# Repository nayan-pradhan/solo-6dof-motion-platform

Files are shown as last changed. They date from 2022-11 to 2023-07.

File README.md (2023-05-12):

# SOLO 6 DoF Motion Platform

motion platform (https://youtu.be/thXPA2MYcQw "6-DoF- Motion Platform")

## <u>Introduction</u>
We present an open-source 6 DoF motion platform capable of producing controlled highly dynamic motion in 3D space. The idea is to flip a quadruped robot, attach a 3D printed platform (holding the payload) to the feet, and using inverse kinematics to move the attached platform in the closed-loop kinematic chain. 12 motors works together to produce high acceleration.

Our design is based on the [open-dynamic-robot-initiative](https://github.com/open-dynamic-robot-initiative).

The platform design, pybullet simulation and robot control framework are fully open source.

1. [Hardware Framework](docs/hardware_framework.md)
2. [Software Framework](docs/software_framework.md)
3. [Setup and Notes](docs/setup_and_notes.md)
4. [Calibration and Usage](docs/calibration_and_usage.md) 
5. [Program Execution](docs/program_execution.md)
6. [Video](https://youtu.be/BtfoymwgIUY)

## <u>About the Creaters</u>
The SOLO 6 DoF Motion Platform was created at the [Dynamic Locomotion Group](https://dlg.is.mpg.de) at the [Max-Planck Institute for Intelligent Systems](https://is.mpg.de) by: 
- Nayan Man Singh Pradhan
- Patrick Frank
- An Mo

## <u>Link to Paper</u>
http://dx.doi.org/10.48550/arXiv.2303.17974

Pradhan, N. M. S., Frank, P., Mo, A., & Badri-Spröwitz, A. (2023). Upside down: affordable high-performance motion platform. arXiv preprint arXiv:2303.17974.

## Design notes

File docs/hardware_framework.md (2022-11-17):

# Hardware Framework

<p align="center">
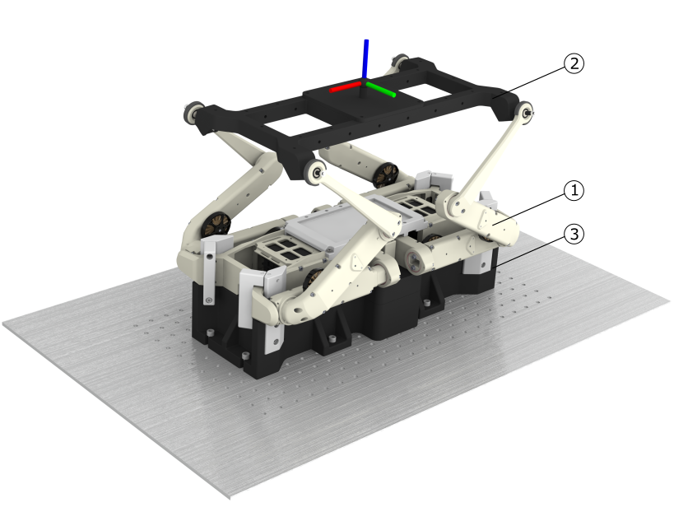
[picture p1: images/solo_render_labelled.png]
  
</p>

The hardware framework consists of three main components: 
1. the [SOLO robot](#solo-robot),
2. the [platform attached to the legs](#platform-attached-to-legs) of the SOLO robot, and
3. the [base component](#base-component) that makes sure the robot is fixed to a table.

The figure above shows the robot fixed to an optic table with the attached platform. The necessary CAD files can be found [here](../resources/CAD_files/).

### 1. SOLO robot
The SOLO 12 Robot is a quadruped robot (assembled from four legs) of total mass $2.2$ kg with a torque-controller for tracking full-body motions computed with a kino-dynamic motion optimizer \cite{herzog2016structured} \cite{ponton2018time}. The brushless actuator module used in the SOLO robot consists of a $9:1$ dual-stage timing belt transmission, a high-resolution optical encoder, and a $5000$ count-per-revolution code wheel mounted directly on the motor shaft. The desired joint torques are converted into desired motor current using the relationship $\tau_{joint}=k_{i}iN$ where $k_{i}=0.025$ Nm/A and the gear reduction $N=9$ leading to a $\tau_{joint}=0.225i$. The actuators can output $\tau_{max}=2.7$ Nm joint torque at $12$ A. More information regarding the SOLO robot can be found in the Open Dynamic Robot Initiative [Website](https://open-dynamic-robot-initiative.github.io) and their [GitHub](https://github.com/open-dynamic-robot-initiative). 
<p align="center">
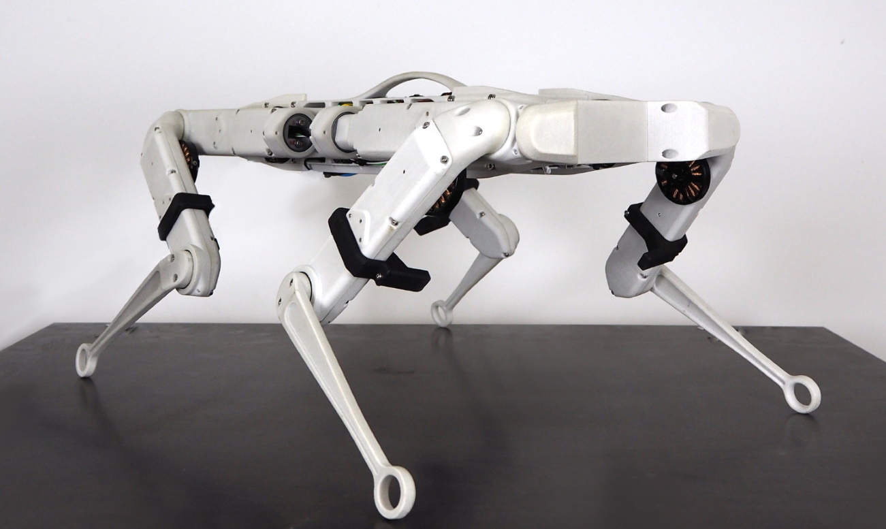
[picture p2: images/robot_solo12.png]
    
</p>
<p align="center">Solo12 Quadruped Robot. Picture source: PAL robotics.</p>

### 2. Platform Attached to Legs
The platform is mounted to the robot by four pins fixed to a spherical bearing. We used the [IGUS KGLM-05](https://www.igus.eu/product/388?C=DE&L=en&artNr=KGLM-05) spherical bearing with a maximum pivot angle of 30 degrees. These spherical bearings are press fitted to the robot legs and secured by M4 nuts on the platform. The platform itself is 3D printed while the pins are machined. There are multiple mounting points provided to attach something to the platform. All parts needed for the platform are shown in the figure below.
<p align="center">
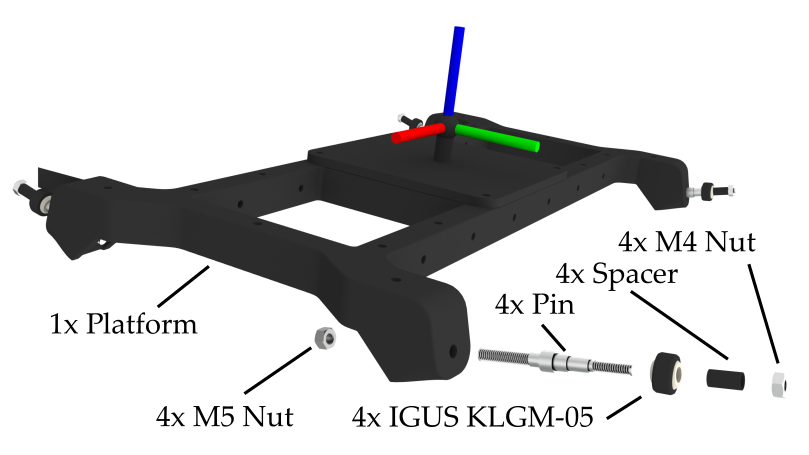
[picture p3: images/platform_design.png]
    
</p>

### 3. Base Component
To fix the robot during movement, we designed a base that is screwed on an optic table. The base consists of multiple parts, as shown in the figure below. We replaced the lower center plate of the robot with our design (No. 2), to be able to fix the robot on the base. The plate gets attached by four M3 and eight M2.5 screws to the robot and six M4 screws to the base. The base itself is fixed to the optic table by eight M6 Screws. To further support the robot base, we design clamps (No. 3, 4, 5, 6) that attach close to the hip of the robot.
<p align="center">
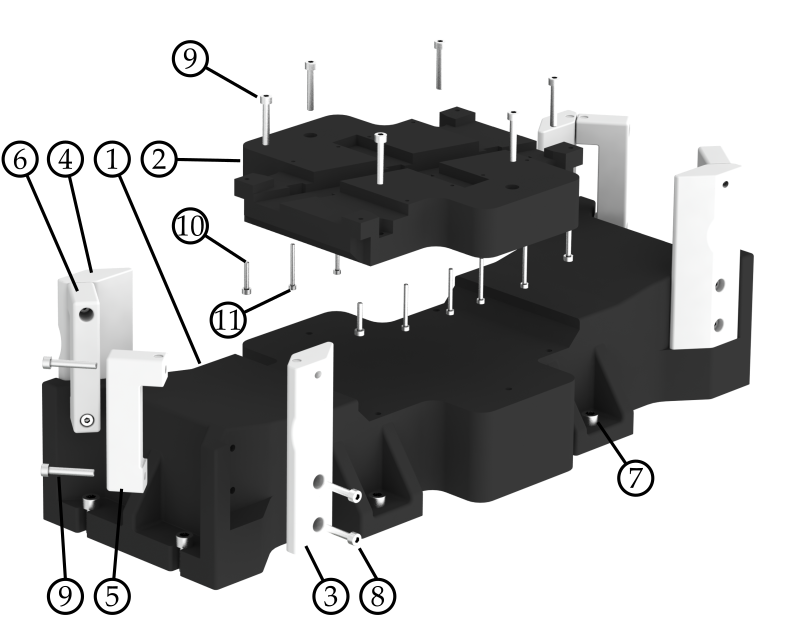
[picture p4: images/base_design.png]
    
</p>

The table below lists all the parts needed to build the base.

| No. | Name | Qty.  |
| :-----: | --- | :---: |
| 1  | Base | 1 |
| 2  | Plate Robot | 1  |
| 3 | Base Clamp | 2 |
| 4 | Base Clamp mirrored | 2 |
| 5 | Robot Clamp | 2 |
| 6 | Robot Clamp mirrored | 2  |
| 7 | SHC Screw M6x16 | 8 |
| 8 | SHC Screw M4x20 | 8 |
| 9 | SHC Screw M4x25 | 14  |
| 10 | SHC Screw M3x16 | 4  |
| 11 | SHC Screw M2.5x25 | 8  |
| 12 | HeliCoil M4 Thread Insert | 22 |

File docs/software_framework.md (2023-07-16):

# Software Framework

Our open-source software package uses the master-board from the SOLO robot [Open Dynamic Robot Initiative GitHub page](https://github.com/open-dynamic-robot-initiative) to send torque commands to the motors and read sensor data. The [master-board](https://github.com/open-dynamic-robot-initiative/master-board) centralises all the sensor and actuator data and provides wired and wireless connection to a real-time computer. 

The primary language used in our software package is Python3. The software framework is built to be modular such that any user may update, add, or remove parts of the module. As long as the modules receive an input csv file of the proper format and output the respective csv files of proper format, the software framework will work as designed. 

Our software framework consists of 4 main modules:
1. [Platform Trajectory Generation](#platform-trajectory-generation)
2. [Inverse Kinematics Tool](#inverse-kinematics-tool)  
3. [Control Environment](#control-environment)  
4. [Post Processing](#post-processing)  

A UML activity diagram showing a high-level overiew of the complete software framework is shown below:
<p align="center">
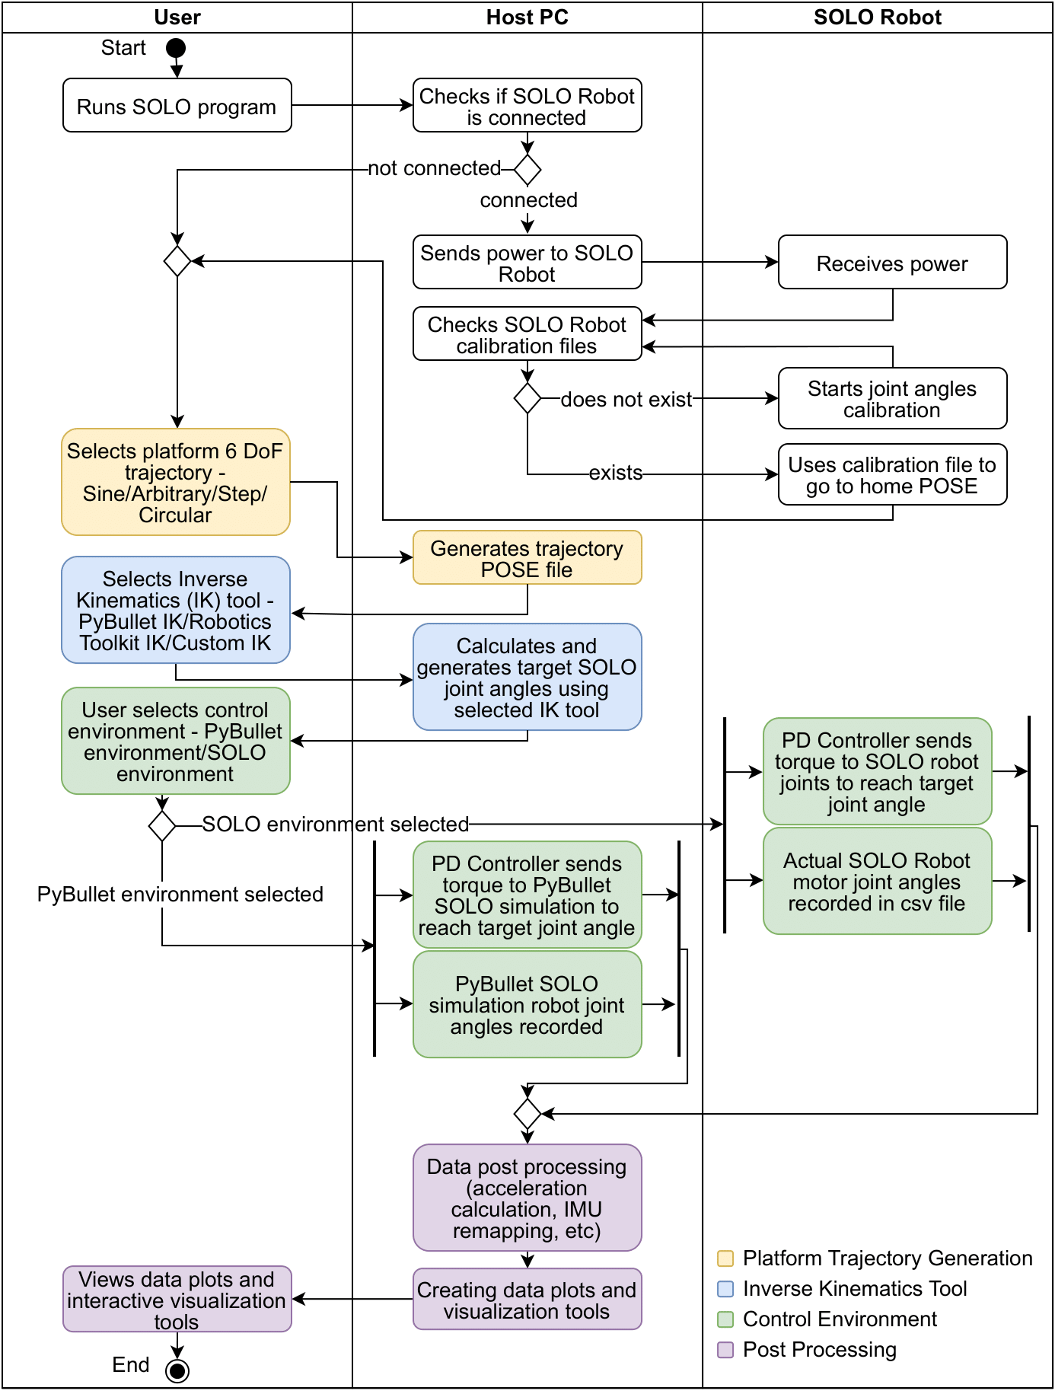
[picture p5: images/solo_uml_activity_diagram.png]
  
</p>

## 1. Platform Trajectory Generation
The Platform Trajectory Generation module generates the target position and target orientation of the platform. A csv file is auto-generated containing a sequence of tx, ty, tz, rx, ry, and rz for translation and rotation in x, y and z respectively. The sequence starts with an initial waiting time of 2 seconds where the platform stays stable in the home position. The sequence is generated for a frequency of $240$ Hz for the PyBullet control environment and $1000$ Hz for the SOLO robot control environment (more details in [Control Environment](#control_environment)). 

The input parameters are given through CSV files located at: [`src/data_files/input_files/`](/src/data_files/input_files/).

We have implemented the following options for trajectory generation: 
- <b>Sine Trajectory Generation:</b> The sine trajectory generation generates a sequence of platform target positions and orientations by taking in the run time for the sequence (seconds), the waiting time after the completion of the sequence (seconds), the direction of movement (x/y/z), the motion type (translation/rotation), the frequency of the sine wave (Hz), the amplitude of the sine wave (mm/deg), and offsets in x, y, and z (mm) axis in case the user wants to modify the axis of translation/rotation. A list of multiple sine sequence inputs can be specified by the user in the same input csv file. 
- <b>Arbitrary Trajectory Generation:</b> The arbitrary trajectory generation generates a sequence of platform target positions and orientations by taking in a sequence of target positions (mm), target orientations (deg), and interpolation times (seconds) with respect to the home position. The trajectory is generated by doing a smooth linear interpolation between the desired target positions and orientations with the specified time of interpolation.  
- <b>Step Trajectory Generation:</b> The step trajectory generation generates a sequence of platform target positions and orientations by taking in a single line of platform end target position (mm) and orientation (deg). The generated trajectory contains a sudden change (in 1 ms) in target position and orientation to generate a step function. This is can be used for tuning the controller. 
- <b>Circular Trajectory Generation:</b> The circular trajectory generation generates a sequence of platform target positions and orientations such that the platform translates and rotates in a circular movement by taking in the radius of translation (mm), the angle of rotation (deg), the number of rounds, the frequency of rotation in each round, the translation and rotation direction (clock-wise/counter-clock-wise), and a flag to enable and/or disable translation and rotation. 

<b>Input:</b> CSV file according to required trajectory at [`src/data_files/input_files/`](/src/data_files/input_files/).  
<b>Output:</b> CSV file with desired target platform position and orientation auto-generated at [`src/data_files/auto_generated/traj_platform.csv`](../src/data_files/auto_generated/traj_platform.csv).  

## 2. Inverse Kinematics Tool
The Inverse Kinematics Tool module takes the auto-generated csv file of platform trajectories generated from section [Platform Trajectory Generation](#platform-trajectory-generation) as the input and calculates the target joint angles for each joint using inverse kinematics. We are using PyBullet for the inverse kinematics calculation. A new csv file is auto-generated that stores the target joint angles for each joint of the SOLO robot. 

<b>Input:</b> Auto-generated CSV file with desired target platform position and orientation from [Platform Trajectory Generation](#platform-trajectory-generation) at [`src/data_files/auto_generated/traj_platform.csv`](../src/data_files/auto_generated/traj_platform.csv).  
<b>Output:</b> CSV file with desired target joint angles for SOLO robot [`src/data_files/auto_generated/traj_joints.csv`](../src/data_files/auto_generated/traj_joints.csv).  

## 3. Control Environment
The Control Environment module takes the auto-generated csv file of target joint angles generated from Section [Inverse Kinematics Tool](#inverse-kinematics-tool) as the input. The controller uses the target joint angles and actual joint angles in order to give torque commands to the motors. Our software framework contains two control environments:
- <b>PyBullet Simulation Environment:</b> The PyBullet Simulation Environment (shown in figure to the left below) runs the 6 DoF SOLO motion platform in $240$ Hz (as it is limited by PyBullet). The simulation environment loads the URDF models of the SOLO robot and the sensor platform and creates constraints between the foot joints and the platform corners. The PyBullet simulation can be used to test various new algorithms and implementations without using the actual SOLO robot.  
- <b>SOLO Environment:</b> The SOLO Environment (shown in figure to the right below) runs the 6 DoF SOLO motion platform (physical) in $1000$ Hz. The SOLO environment initializes the SOLO robot (according to the master-board code), calibrates the SOLO robot (more details shared in [setup_and_usage.md](setup_and_usage.md), executes the desired motion trajectory, and reads/stores the IMU, motors, and sensor data. The PD controller gains can be updated if required. 

<p align="center">
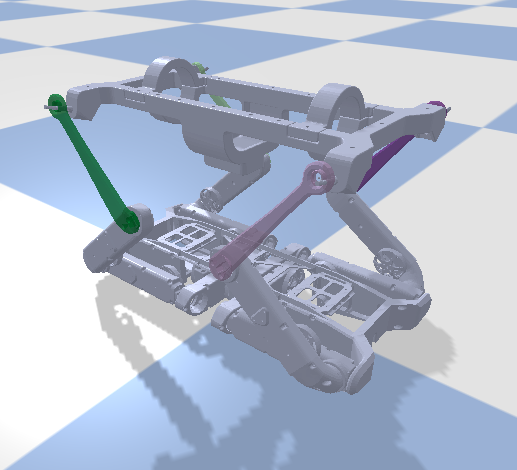
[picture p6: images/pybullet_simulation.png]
  
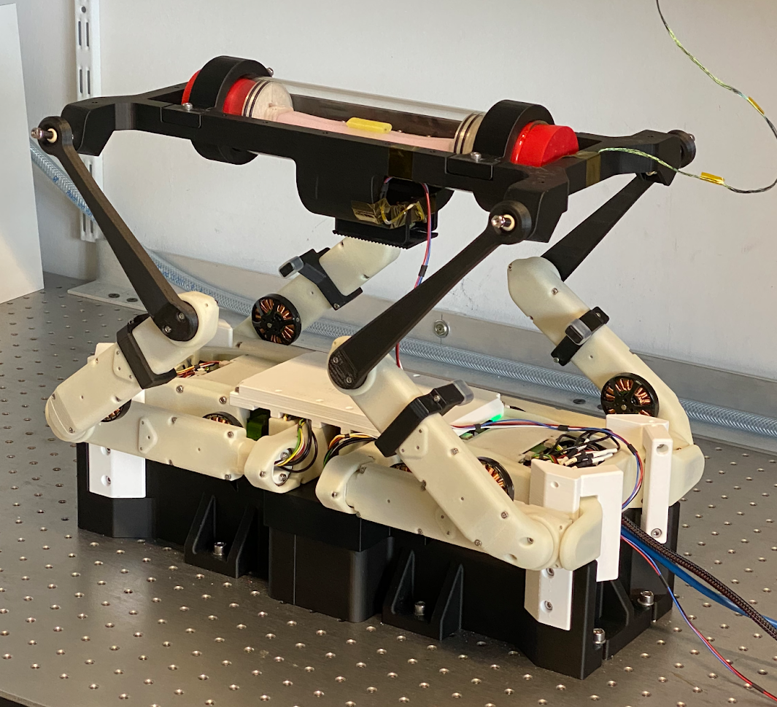
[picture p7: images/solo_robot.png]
   
</p>

<b>Input:</b> CSV file with desired target joint angles for SOLO robot from [Inverse Kinematics Tool](#inverse-kinematics-tool) at [`src/data_files/auto_generated/traj_joints.csv`](../src/data_files/auto_generated/traj_joints.csv).  
<b>Output:</b> Robot motion (simulation or physical) and CSV file with all data collected at [`src/data_files/output_files`](../src/data_files/output_files). 

## 4. Post Processing
The final module in the software architecture is the Post Processing module. The Post Processing module contains two main parts:
- <b>Data Processing:</b> The Data Processing module reads and loads the data csv files saved in tbe above sections. A method to calculate the position and orientation at the center of the platform based on the robot joint angles using forward kinematics has been implemented. The linear and angular velocity and linear and angular acceleration of the platform is also derived using the position and orientation of the platform. This provides the option for a user to get the position, velocity, and acceleration at the platform without investing in an expensive IMU. We use these calculations in order to test and compare with the IMU data. The calculated platform position, orientation, linear velocity, angular velocity, linear acceleration, and angular acceleration are filtered using a butter lowpass filter of fixed cutoff frequency of $50$ Hz and sample frequency of $1000$ Hz in order to get smoother results. In addition, methods to transform the IMU data (angular velocity and linear acceleration) from the IMU position to the center of the platform is also present as this is essential for our research. The  Depending on the project and desired results, this section can be used, modified, or ignored. A zoomed-in plot showing the calculated, target, and measured IMU angular velocity for rotation in x-axis and translation in x-axis is shown below. All data is stored into a csv file that can be updated by the user based on the research, project, available resources, and desired outcome. The data preview module is loaded automatically after.
<p align="center">
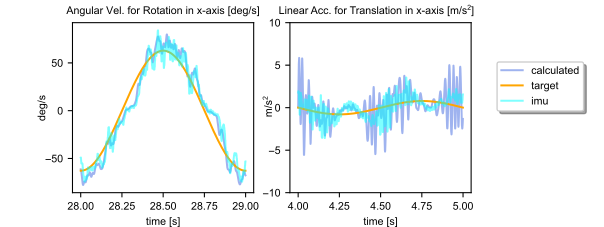
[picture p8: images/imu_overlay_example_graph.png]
  
</p>

- <b>Data Preview:</b> The Data Preview module is responsible of loading data from the stored csv files and plotting plots and graphs depending on the research, project, and desired outcome. The data preview module is called automatically at the end of the program. It can also be executed independently for quick visualization of the latest data. An example summary plot showing the calculated and target platform position and orientation when commanded x,y,z translation and rotation is shown below.

<p align="center">
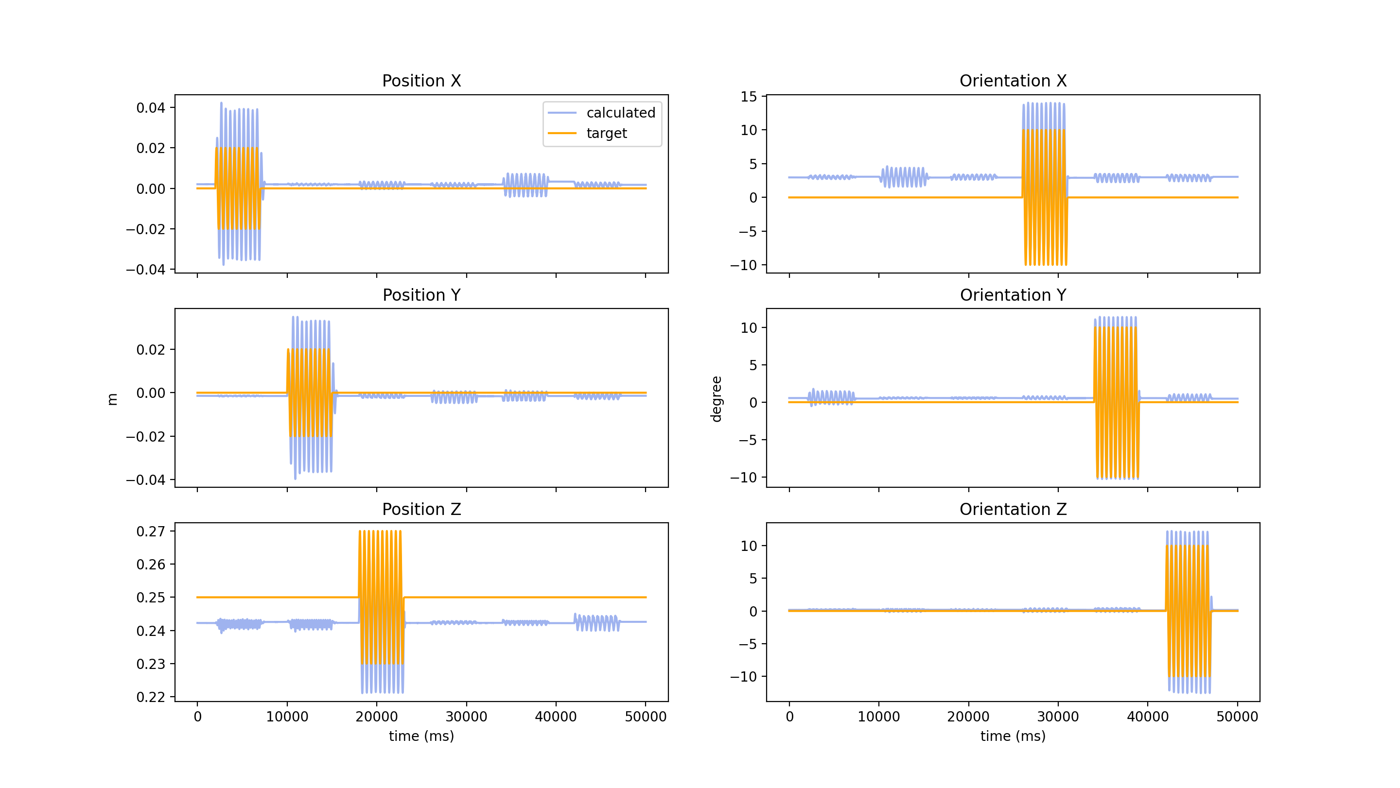
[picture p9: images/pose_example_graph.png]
  
</p>

<b>Input:</b> CSV file with all data collected from [Control Environment](#control-environment) at [`src/data_files/output_files`](../src/data_files/output_files).  

<b>Output:</b> Summary Plots and Graphs.

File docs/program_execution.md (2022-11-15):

# Program Execution

The software package can be executed using the Command Line Interface or the In-line Terminal Interface. 

## Command Line Interface
The command line interface offers a step-by-step interface that prompts the user for inputs on what program configuration the package should run. This method is convenient and recommended for users who are not familir with the software package.

`cd src`  
`bash start_program.sh`

### Example:
Example of running software configuration for: 
- Sine Sequence
- Pybullet Inverse Kinematics
- Solo Control Environment
- Phase 2 Calibration

<p align="center">
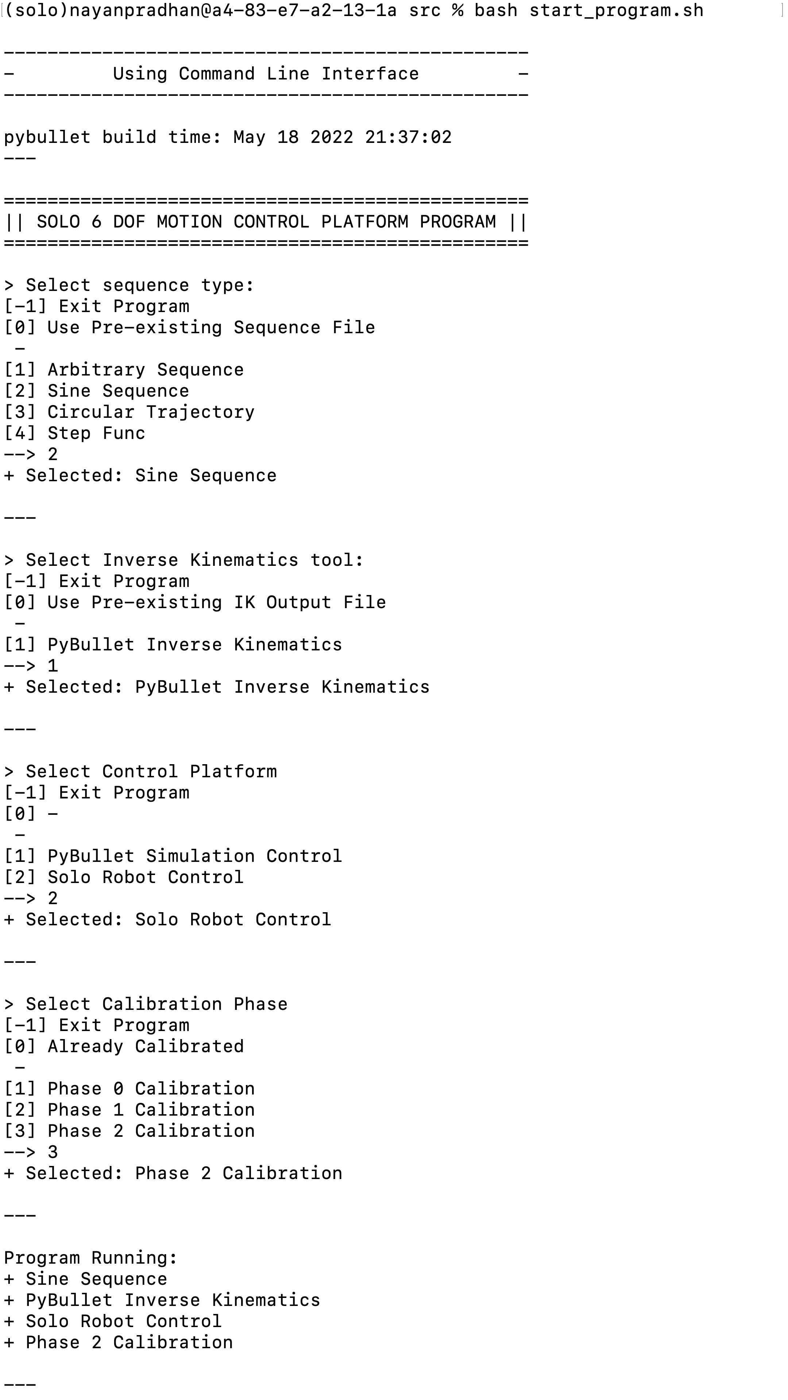
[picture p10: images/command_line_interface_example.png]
  
</p>

---

## In-line Terminal Interface
The in-line terminal interface offers a one line quick and repeatable flag based command system for users who are familiar with the software package.

`cd src`  
`bash start_program.sh <flags>`

### In-line Terminal Interface `<flags>`
`-h`     Print help.  

`-s`     Define sequence type.  
&emsp; `0`   Use pre-existing sequence  
&emsp; `a`   Use arbitrary sequence  
&emsp; `s`   Use sine sequence  
&emsp; `c`   Use circular sequence  
&emsp; `t`   Use step sequence  
    
`-i`     Define inverse kinematics tool.  
&emsp;  `0`   Use pre-existing inverse kinematics  
&emsp;  `p`   Use pybullet inverse kinematics  
    
`-c`    Define control environment.  
&emsp; `p`   Use pybullet environment  
&emsp; `s`   Use solo robot environment  
    
`-p`     Define calibration phase.  
&emsp; `x`   Use no calibration  
&emsp; `0`   Calibration Phase 0  
&emsp; `1`   Calibration Phase 1  
&emsp; `2`   Calibration Phase 2   

### Example:
Example of running software configuration for: 
- Sine Sequence
- Pybullet Inverse Kinematics
- Solo Control Environment
- Phase 2 Calibration

<p align="center">
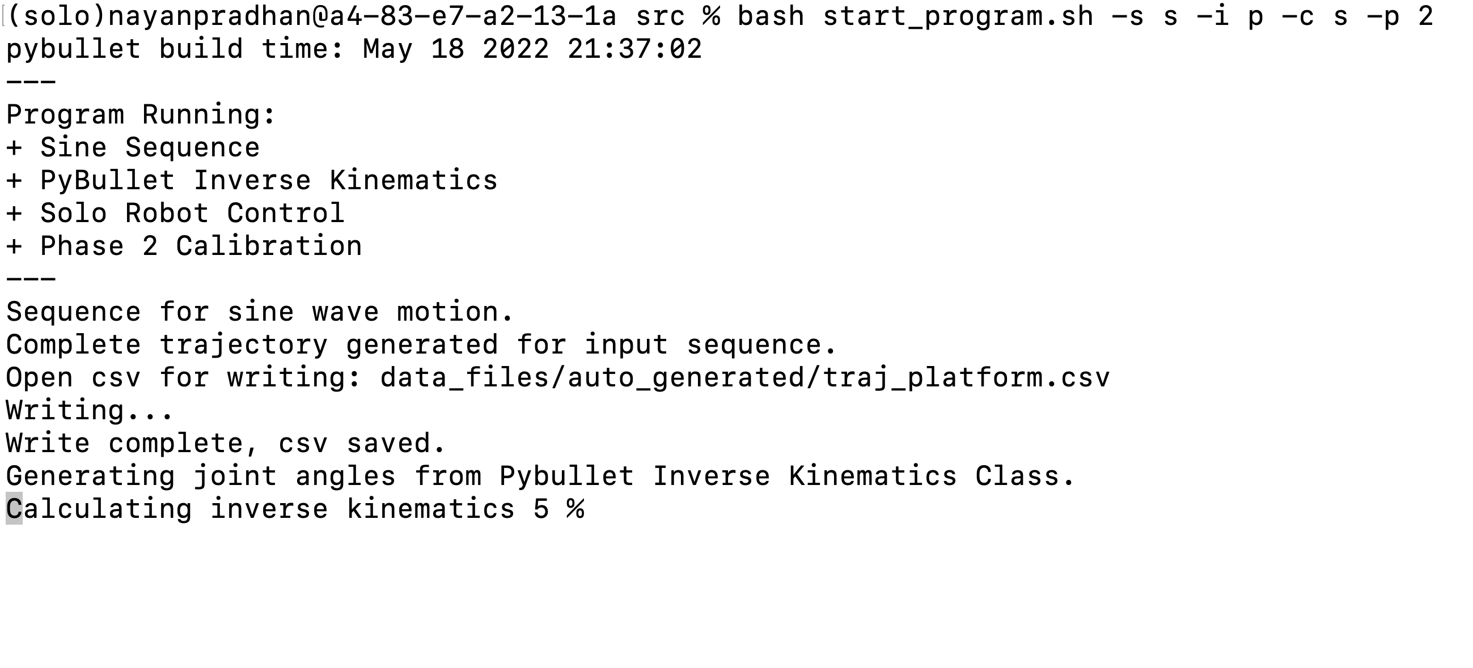
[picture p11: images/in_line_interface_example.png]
  
</p>

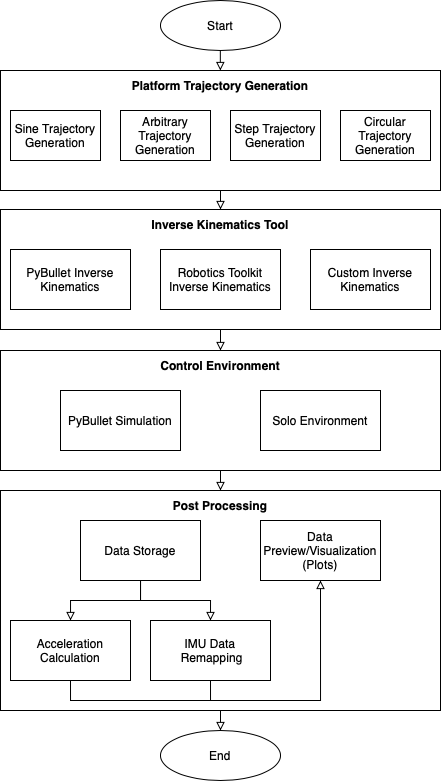
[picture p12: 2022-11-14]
images/solo-6dof-motion-platform_framework.png

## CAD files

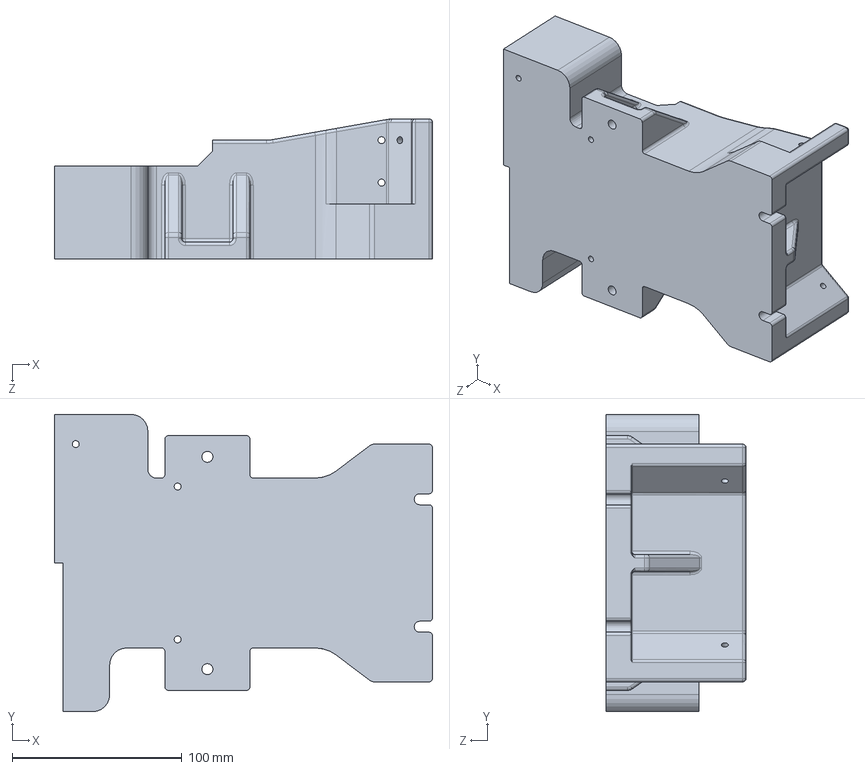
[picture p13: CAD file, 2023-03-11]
resources/CAD/base/fixture_plate_main_for_Printing_1.SLDPRT
222.5 x 175.0 x 82.5 mm

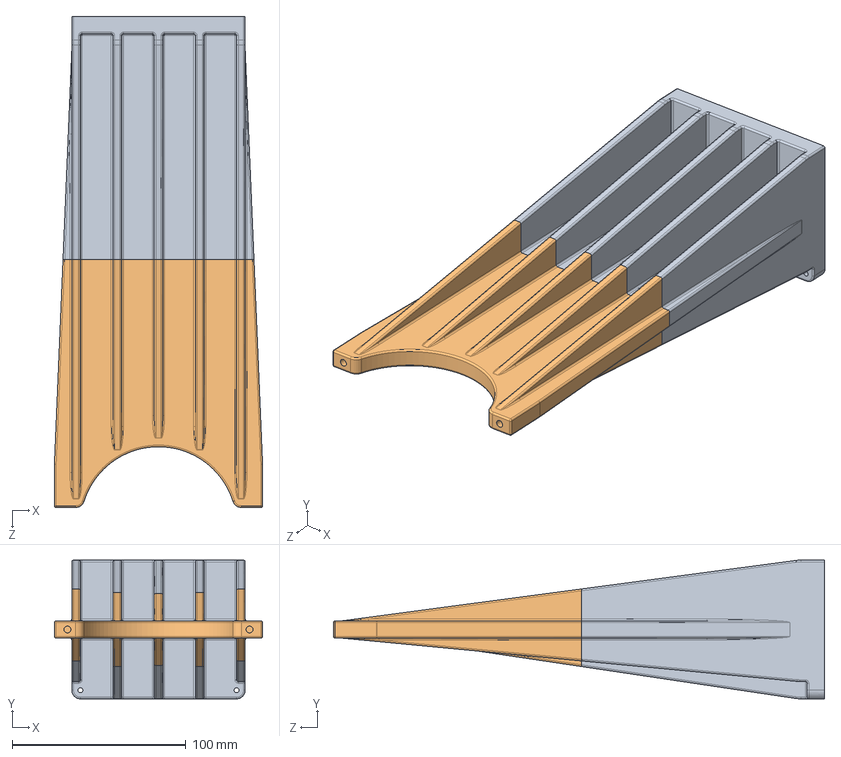
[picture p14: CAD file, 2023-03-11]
resources/CAD/calibration_tools/calibration_platform_2022-08-09.SLDASM
120.0 x 80.0 x 283.0 mm
calibration_platform
calibration_platform_upper

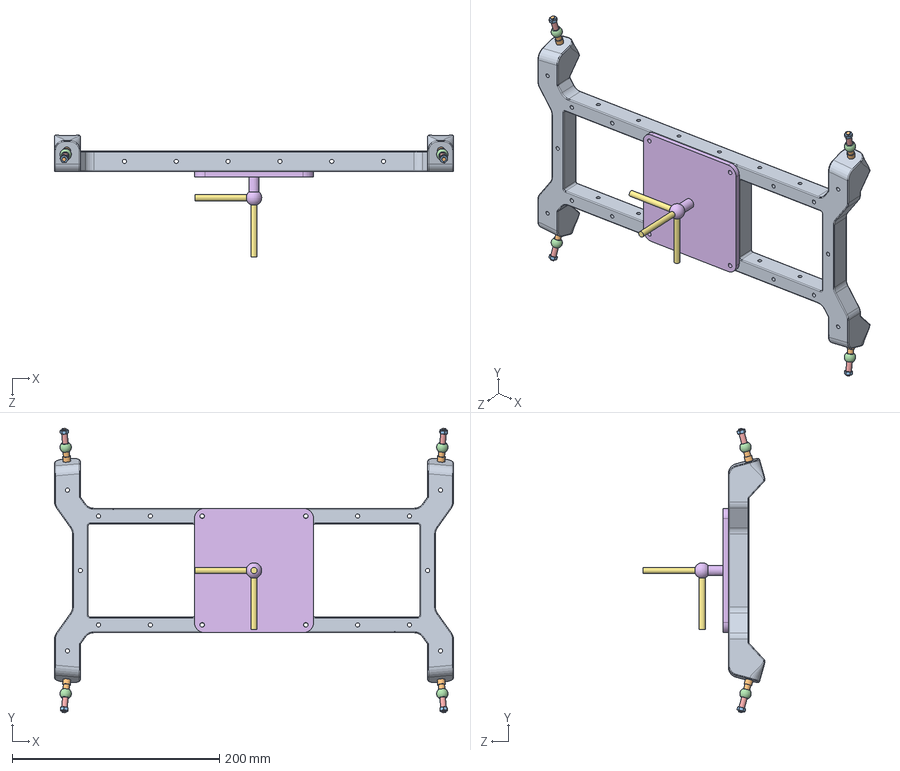
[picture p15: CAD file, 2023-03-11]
resources/CAD/platform/platform.SLDASM
384.9 x 274.5 x 117.3 mm
demo_platform_2022-10-06
pin_ball_bearing_2022-06-03 x 4
hex nut style 1 gradeab_din x 8
IGUS_KGLM-05_inner_shell x 4
tube_ball_bearing_2022-06-07 x 4
demo_platform_coordinate_system
demo_platform_axis x 3

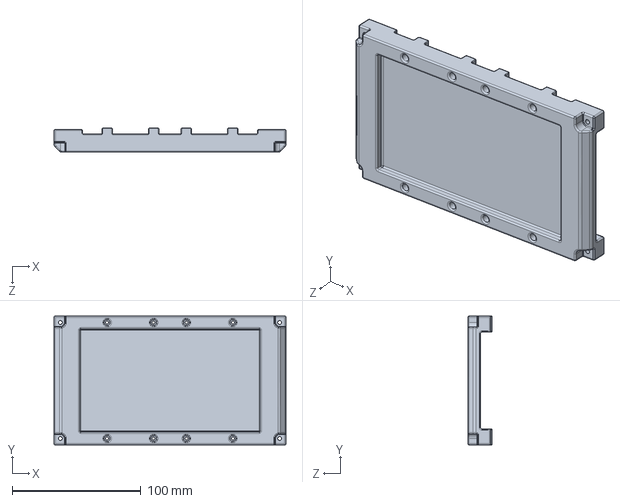
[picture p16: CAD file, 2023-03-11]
resources/CAD/base/mechanical_hardstop_2022-08-04.SLDPRT
180.0 x 100.0 x 19.0 mm

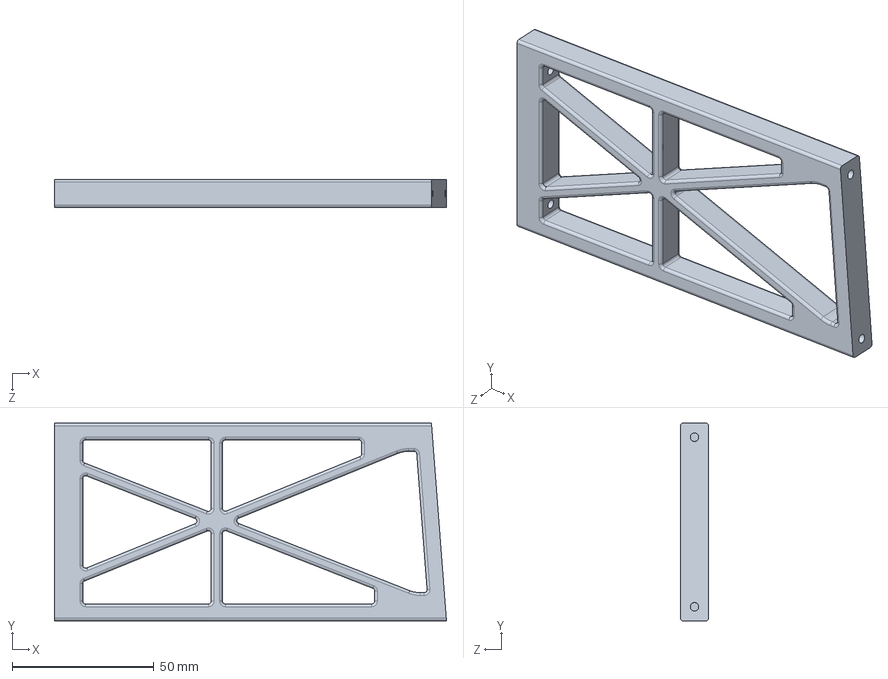
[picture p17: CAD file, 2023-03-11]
resources/CAD/calibration_tools/calibration_tool_motion_simulator_connector_mirror.SLDPRT
138.3 x 69.8 x 10.0 mm

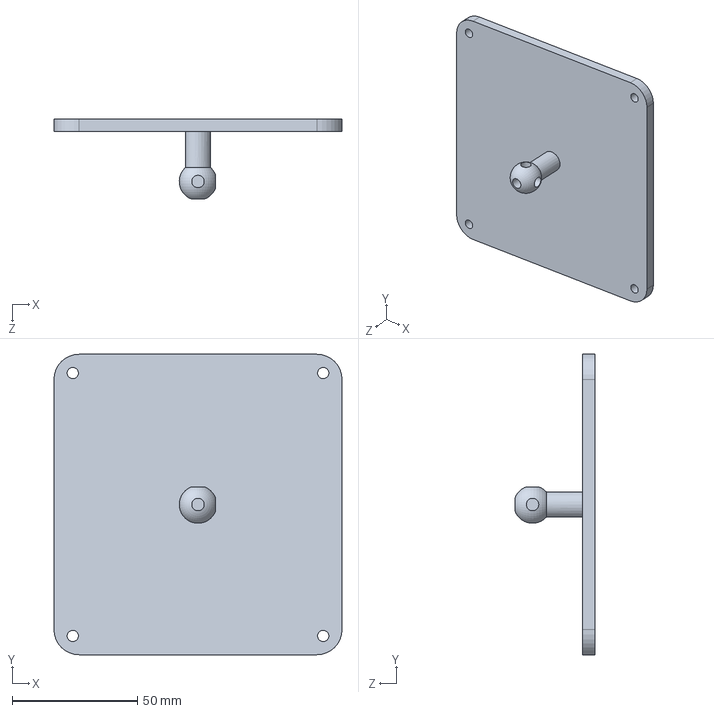
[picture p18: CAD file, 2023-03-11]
resources/CAD/platform/demo_platform_coordinate_system.SLDPRT
115.0 x 120.0 x 32.1 mm

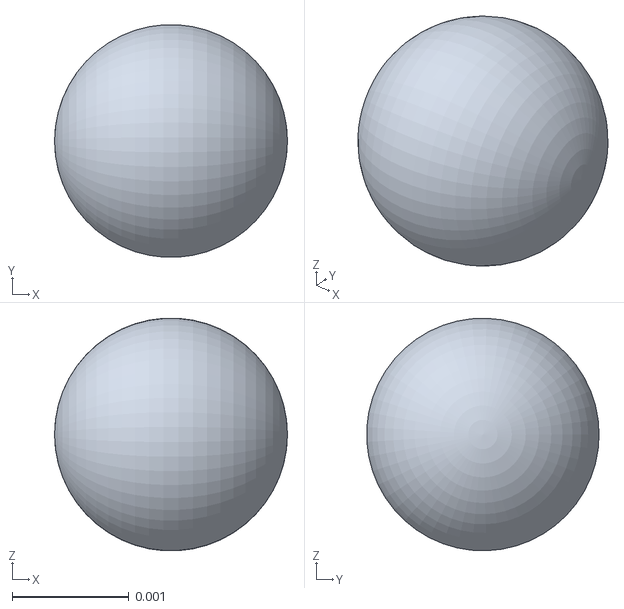
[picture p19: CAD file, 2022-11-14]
resources/URDF/URDF_motion_simulator_simplified_dummy/meshes/dummy_left_front.STL
0.002 x 0.00199 x 0.002

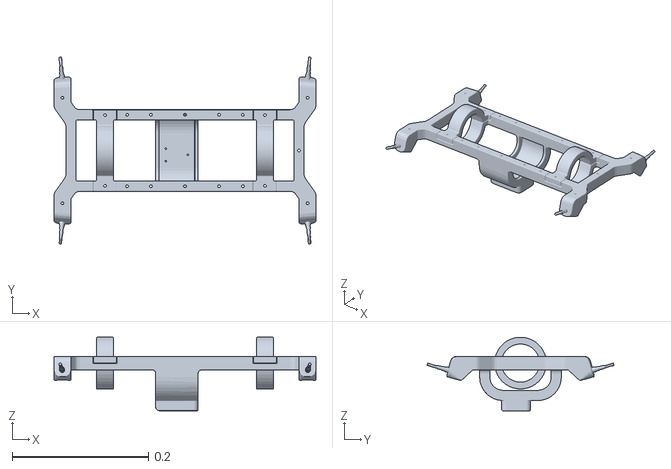
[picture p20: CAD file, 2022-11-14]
resources/URDF/URDF_sensor_platform_simplified/meshes/base_link.STL
0.385 x 0.274 x 0.108

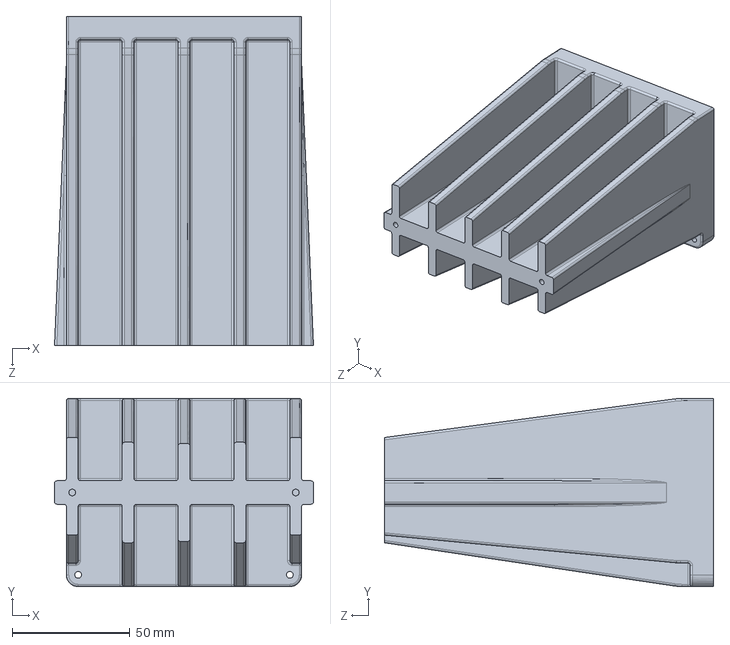
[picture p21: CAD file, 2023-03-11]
resources/CAD/calibration_tools/calibration_platform.SLDPRT
110.1 x 80.0 x 140.0 mm

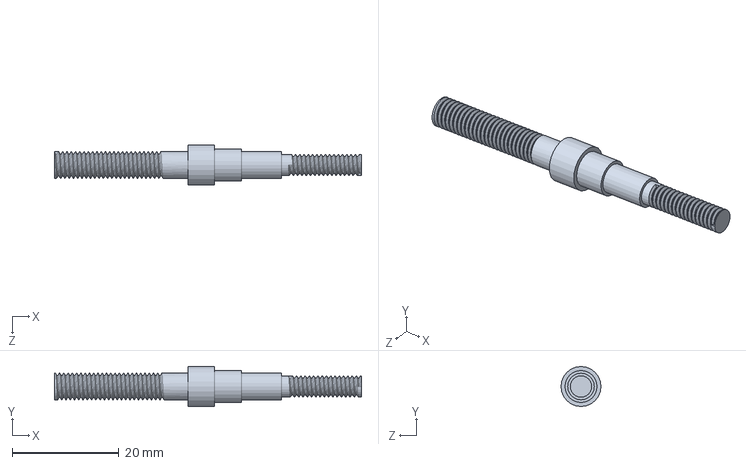
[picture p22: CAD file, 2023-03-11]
resources/CAD/platform/pin_ball_bearing_2022-06-03.SLDPRT
57.5 x 7.50 x 7.50 mm

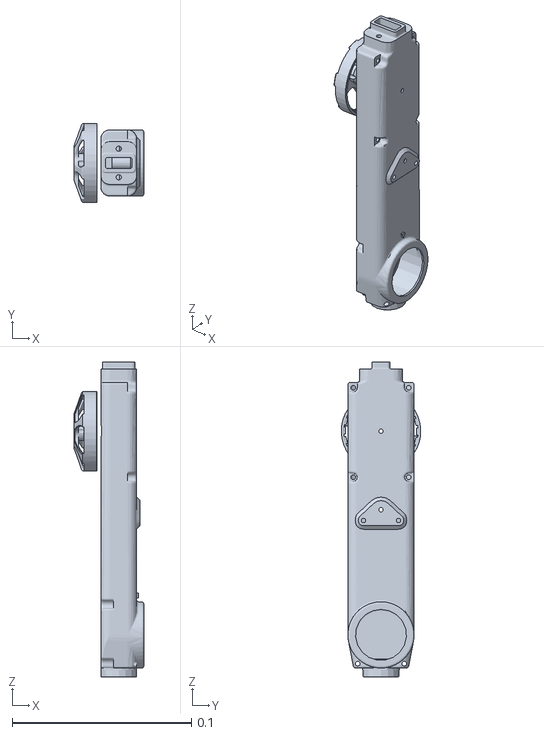
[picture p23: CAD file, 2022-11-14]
resources/URDF/URDF_motion_simulator_simplified_dummy/meshes/hip_right_front.STL
0.0389 x 0.0444 x 0.176

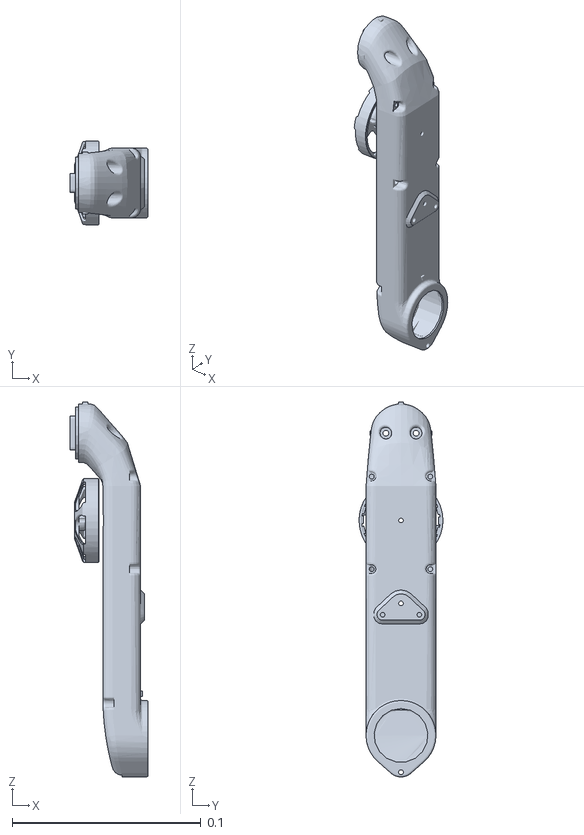
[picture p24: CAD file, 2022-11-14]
resources/xacro/URDF_motion_simulator_simplified_dummy/meshes/upper_leg_left_back.STL
0.0415 x 0.0444 x 0.198

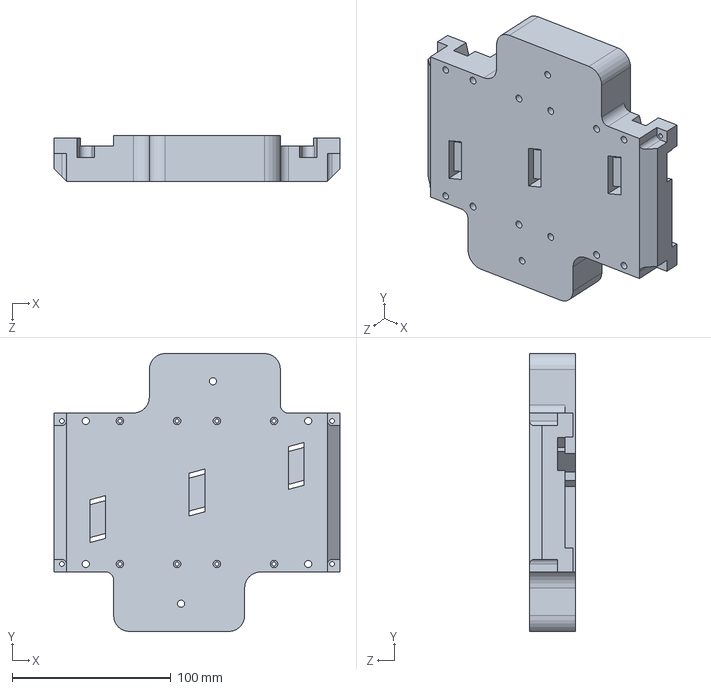
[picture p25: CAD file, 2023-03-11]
resources/CAD/base/fixture_plate_robot_2022-05-10.SLDPRT
180.0 x 175.0 x 29.0 mm

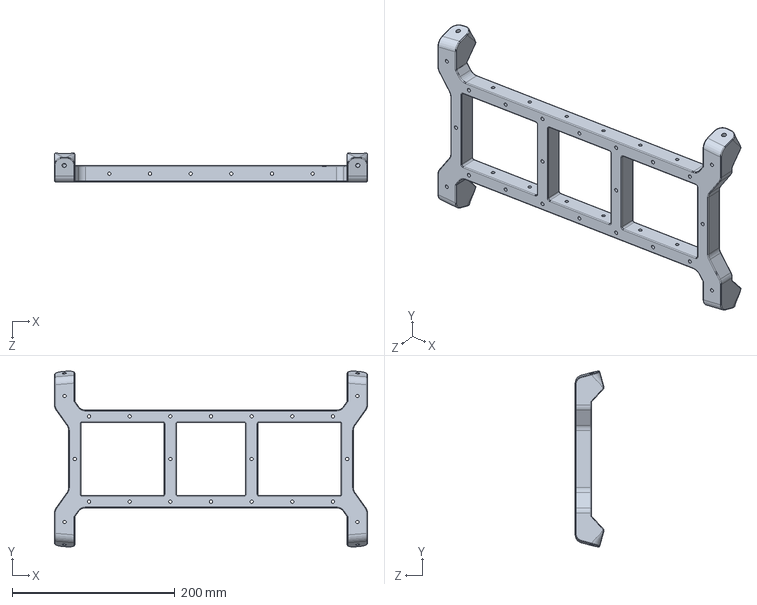
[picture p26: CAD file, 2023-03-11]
resources/CAD/platform/demo_platform_2022-10-06.SLDPRT
384.9 x 216.3 x 35.3 mm

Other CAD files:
resources/CAD/base/fixture_plate_main_for_Printing_2.SLDPRT
resources/URDF/URDF_motion_simulator_simplified_dummy/meshes/hip_left_back.STL
resources/xacro/URDF_motion_simulator_simplified_dummy/meshes/dummy_right_back.STL
resources/CAD/calibration_tools/Body1.SLDPRT
resources/CAD/calibration_tools/calibration_platform_upper.SLDPRT
resources/CAD/calibration_tools/calibration_tool_motion_simulator.SLDPRT
resources/CAD/calibration_tools/calibration_tool_motion_simulator_connector.SLDPRT
resources/CAD/calibration_tools/calibration_tool_motion_simulator_mirror.SLDPRT
resources/CAD/platform/IGUS_KGLM-05_inner_shell.SLDPRT
resources/CAD/platform/demo_platform_axis.SLDPRT
resources/CAD/platform/tube_ball_bearing_2022-06-07.SLDPRT
resources/URDF/URDF_motion_simulator_simplified_dummy/meshes/dummy_left_back.STL
resources/URDF/URDF_motion_simulator_simplified_dummy/meshes/dummy_right_back.STL
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

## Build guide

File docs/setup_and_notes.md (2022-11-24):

# Setup and Notes

1. [Hardware Setup](#hardware-setup)
2. [Software Setup](#software-setup)
3. [Realtime OS Setup](#realtime-os-setup)
4. [Known Issues and Solutions](#known-issues-and-solutions)
5. [Notes](#notes)

---

### Hardware Setup
1. Refer to the [Open Robot Quadruped Robot 12 DoF](https://github.com/open-dynamic-robot-initiative/open_robot_actuator_hardware/blob/master/mechanics/quadruped_robot_12dof_v1/README.md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) for setting up the SOLO 12 Robot.
2. Refer to the [Hardware Framework](docs/hardware_framework.md) page for instructions on setting up the motion platform environment. 

---

### Software Setup
1. Get and setup the [Open Dynamic Robot Initiative Masterboard SDK](https://github.com/open-dynamic-robot-initiative/master-board/blob/master/sdk/master_board_sdk/README.md) interface.
2. Clone the `solo-6dof-motion-platform` repository. 
    ```
    git clone https://github.com/nayan-pradhan/solo-6dof-motion-platform
    ```
3. Clone the Open Dynamic Robot Initiative Masterboard Git repository inside `solo-6dof-motion-platform/resources/`. 
    ```
    cd solo-6dof-motion-platform/resources/
    git clone --recursive https://github.com/open-dynamic-robot-initiative/master-board.git
    ```
4. Setup, build, and install necessary modules for the master-board package.
    ```
    cd master-board/sdk/master_board_sdk
    mkdir build
    cd build
    cmake -DBUILD_PYTHON_INTERFACE=ON -DCMAKE_BUILD_TYPE=Release -DPYTHON_EXECUTABLE=$(which python3) ..
    make
    sudo PYTHONPATH=./master-board/sdk/master_board_sdk/build pip3 install pybullet pynput
    ```

---

### Realtime OS Setup

#### Install Linux and preempt RT patch.
1. Download and install Ubuntu. 
2. Install required dependencies.
    ```
    sudo apt install -y flex bison libssl-dev libelf-dev libncurses5-dev
    ```
3. Check kernel version. We are using version 5.15.0.
    ```
    uname -r
    ```
4. Download preempt RT patch (.patch.xz file) for your kernel version via this [link](https://wiki.linuxfoundation.org/realtime/preempt_rt_versions). We take the latest 5.15 kernel patch.
5. Download the kernel matching the preempt RT patch you just downloaded (.tar.xz file) via this [link](https://mirrors.edge.kernel.org/pub/linux/kernel/)
6. Extract the downloaded files.
    ```
    cd ~/Downloads/
    xz -d linux-YOURVERSION.tar.xz
    xz -d patch-YOURVERSION.patch.xz
    tar xf linux-YOURVERSION.tar
    ```
7. Change directory to kernel directory and apply patch. 
    ```
    cd linux-YOURVERSION/
    patch -p1 < ../patch-YOURVERSION.patch
    ```
8. Configure kernel.
    ```
    cp -v /boot/config-$(uname -r) .config
    make oldconfig
    ```
    For Preemption model choose: Fully Preemptible Kernel (Real-Time). For the rest use default settings by pressing enter.
    ```
    scripts/config --disable SYSTEM_TRUSTED_KEYS
    make x86_64_defconfig
    ```
9. Compile and install kernel.
    ```
    sudo make deb-pkg
    sudo make modules_install
    sudo make install
    ```
10. Update grub. 
    ```
    sudo update-initramfs -c -k YOURVERSION
    sudo update-grub
    ```
11. Reboot your system. 

#### Update Nvidia Driver
First try the easier way to install the driver, but it is not possible on some systems.
1. Download latest Nvidia driver from the [Nvidia website](https://www.nvidia.com/download/index.aspx).
2. Go to your Downloads folder, make file executable, and run the file. 
    ```
    cd ~/Downloads/
    chmod +x ./NVIDIAFILE.run
    sudo ./NVIDIAFILE.run
    ```
If this is not working and you get the error 'x server is running' or the message that Nvidia drivers will not work on realtime systems, try the following steps:
1.  Press Ctrl+Alt+F1 to open a Terminal and login with your credentials.
2.  Stop X-Server. 
    ```
    sudo systemctl stop lightdm
    ```
3. Install the driver. 
    ```
    cd ~/Downloads/
    sudo IGNORE_PREEMPT_RT_PRESENCE=1 bash ./NVIDIAFILE.run
    ```
4. Start X-Server.
    ```
    sudo systemctl start lightdm
    ```
5. Reboot your system. 

#### Configure your System
1. Create 'realtime' group and add users.
    ```
    sudo groupadd realtime
    sudo usermod -aG realtime <username>
    ```
2. Set rtprio and memlock limits.
    ```
    sudo tee /etc/security/limits.d/99-realtime.conf > /dev/null <<EOL
    @realtime - rtprio 99
    @realtime - memlock unlimited
    EOL
    ```
3. Reboot your system. 

--- 

### Known Issues and Solutions

- #### Beeping sound from motor drivers
    **_Issue:_** Robot motor drivers beep when starting up bash script. This issue usually occurs when testing with the robot is done for a very long time or if the power supply has been turned ON for a very long time (3-4 hours). The masterboard also gets very warm.  
    **_Solution:_** Turn the power supply OFF for a few minutes (around 10-15 minutes) and restart the power supply when the masterboard is cool to touch.

- #### Robot timeout/motor drivers red blinking lights  
    **_Issue:_** Robot times out and the motor drivers start blinking red lights. This issue usually occurs when the motors do not receive a new command for more than 1 milli-second. We experienced this issue when we were trying to append new data into a 2-dimensional array and when we tried printing multiple lines in the main loop.  
    **_Solution:_** Avoid running tasks that take a lot of time (eg. appending into 2-dimensional array, printing multiple lines in each iteration, etc) in the main loop.

- #### Wrong motor index found
    **_Issue:_** Sometimes the correct motor indices are not found in the calibration step. If the correct motor indices are not found, the motors will have an offset of . This issue happens if the robot is not setup properly for Calibration Phase 2.  
    **_Solution:_** If you see that the correct motor is not found (motor has an offset of ), immediately stop the program and redo Calibration Phase 2. Make sure the robot motor joints are in the correct 'Calibration Position' as shown in Robot Positions/Configurations.

- #### Robot does unexpected sudden movement at startup
    **_Issue:_** Stop the program immediately if the robot does unexpected sudden movements at startup. This is usually a result of not following the calibration steps properly.  
    **_Solution:_** Re-do the calibration steps carefully. Make sure proper motor indices are saved in the csv files.

---

### Notes   
- To give edit access of output history files to user, do `sudo chown user:user \*` in `data_files/*/history/` directory.

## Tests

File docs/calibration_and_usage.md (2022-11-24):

# Calibration and Usage

1. [Calibration Process](#calibration-process)
2. [Robot Behaviour](#robot-behaviour)
3. [Robot Positions](#robot-positions)

---

### Calibration Process
Calibration is essential for using the physical SOLO robot motion platform. 

#### Calibration Phase 0
Phase 0 calibration initializes the motors and the masterboard. The goal of phase 0 calibration is to use the calibration tools to initialize the robot motors at the [zero position](#zero-position). The program ends automatically after completion of calibration phase 0. This step should take less than 5 seconds. Please restart power supply and re-do phase 0 if it takes more than 5 seconds.
**Steps:**
1. Attach calibration tools with power supply OFF.
2. Turn power supply ON. 
3. Run the program with the phase 0 calibration flag. The flags for the type of sequence and inverse kinematics does not matter in this step. 
    ```
    bash start_program.sh -s 0 -i 0 -c s -p 0
    ```
4. Remove calibration tools. Keep power supply ON.

#### Calibration Phase 1
Phase 1 calibration should be executed after phase 0 calibration. Phase 1 calibration finds the indices of the motors from the zero position (set at phase 0). Phase 1 calibration moves all the four hip motors, lower leg motors, and upper leg motors in a synchronized manner until either all the four corresponding motor indices are found or until the set maximum and minimum motor angle variable is reached in both directions respectively. Currently, the maximum motor angle is 25&deg; and minimum motor angle is -25&deg;. If all motor indices are found, the final indices calibration array is saved in the csv file: `src/data_files/calibration_files/solo_phase1_calibrated_offsets.csv`. If all motor indices are not found, there is something wrong in the calibration step. Turning OFF and then turning ON the power supply and re-doing the calibration process (from phase 0) should solve the issue. After saving the motor indices, the motion platform is smoothly placed on the robot body by the `smooth_landing` method. The program ends automatically after completion of calibration phase 1.

After completing phase 1 once, the csv file: 'src/data_files/calibration_files/solo_phase1_calibrated_offsets.csv' should be filled. If no changes are made to the hardware of the robot, phase 0 and phase 1 do not need to be repeated as long as the csv file: 'src/data_files/calibration_files/solo_phase1_calibrated_offsets.csv' is filled.
**Steps:**
1. Make sure the calibration tools are removed.
2. After calibration tools are removed, run the script with the phase 1 calibration flag. The flags for the type of sequence and inverse kinematics does not matter in this step. 
    ```
    bash start_program.sh -s 0 -i 0 -c s -p 1
    ```
3. Turn power supply OFF.

#### Calibration Phase 2
Phase 2 calibration should be executed only after the csv file: 'src/data_files/calibration_files/solo_phase1_calibrated_offsets.csv' is filled. It is important to only start phase 2 calibration when the motor joints are close to the zero position (from phase 0). Therefore, the platform has to be lifted all the way up. This position is called the [calibration position](#calibration-position). The calibration tools should NOT be attached. The power supply must be off when the motors are moved to the calibration position. After the motors are in the calibration position, the power supply should be turned on and the script can be executed. Calibration phase 2 finds the new current motor indices (they are different because every time the power supply is turned ON, it saves that position as the zero position), calculates the offset to the calibrated motor indices from phase 1 calibration, saves the landing position using the free solo control mode, and finally uses the offset such that the zero position is always maintained and consistent. The offset values from calibration phase 2 are saved in the csv file: 'src/data_files/calibration_files/solo_phase2_calibrated_offsets.csv' and the landing position is saved in the csv file: 'src/data_files/calibration_files/solo_landing_pos.csv'.
**Steps:**
1. Make sure the calibration tools are removed.
2. Make sure the power supply is OFF.
3. Manually lift the platform high up such that the robot and motors are in the calibration position.
4. After robot and motors are in the calibration position, turn power supply ON.
5. Run the script with the phase 2 calibration flag. The flags for the type of sequence and inverse kinematics does not matterr in this step too. After completing calibration phase 2, the robot goes into the free solo control mode. 
    ```
    bash start_program.sh -s s -i p -c s -p 2
    ```
6. After finding the calibration indices in phase 2, the robot interpolates to the proper calibrated zero position and starts the free solo control class. This allows the user to move the platform around without the exerting any external torque. 
7. When you start to see the joint angles printing in the screen, move the platform to the [landing position](#landing-position). 
8. After the platform is set to the  [landing position](#landing-position), press the ADC trigger button. This will save the landing position (with the offset) into the csv file: 'src/data_files/calibration_files/solo_landing_pos.csv'.
9. Press `ctrl+c` to exit from the program.

It is important to run calibration phase 2 once every time after the power supply is restarted. If the power supply has not been restarted and if calibration phase 2 has already been executed once at the start of this test run, there is no need to run the calibration phase 2 again. After completing phase 2 once, you can run the steps below without having to manually adjust the position of the platform or robot. 

#### Calibration Phase X
**Steps if calibration step 2 has already been executed once after power supply has been turned ON:**
1. Make sure that calibration phase 2 has already been executed once at the beginning of the current test run.
2. The solo robot should be in [landing position](#landing-position).
3. The power supply should be ON. If power supply is OFF, you must run calibration phase 2 as detailed above and you should not continue with the steps below.
4. If power supply is ON, you can run the script with the no calibration flag. If you have already generated your motion trajectory, you can use the pre-existing inverse kinematics flag. If not, use the flags according to the platform motion you want to execute. 
    ```
    bash start_program.sh -s s -i p -c s -p x
    ```

---

### Robot Positions
#### Zero position
Configuration of Robot when calibration tools are attached at Calibration Phase 0.
<p align="center">
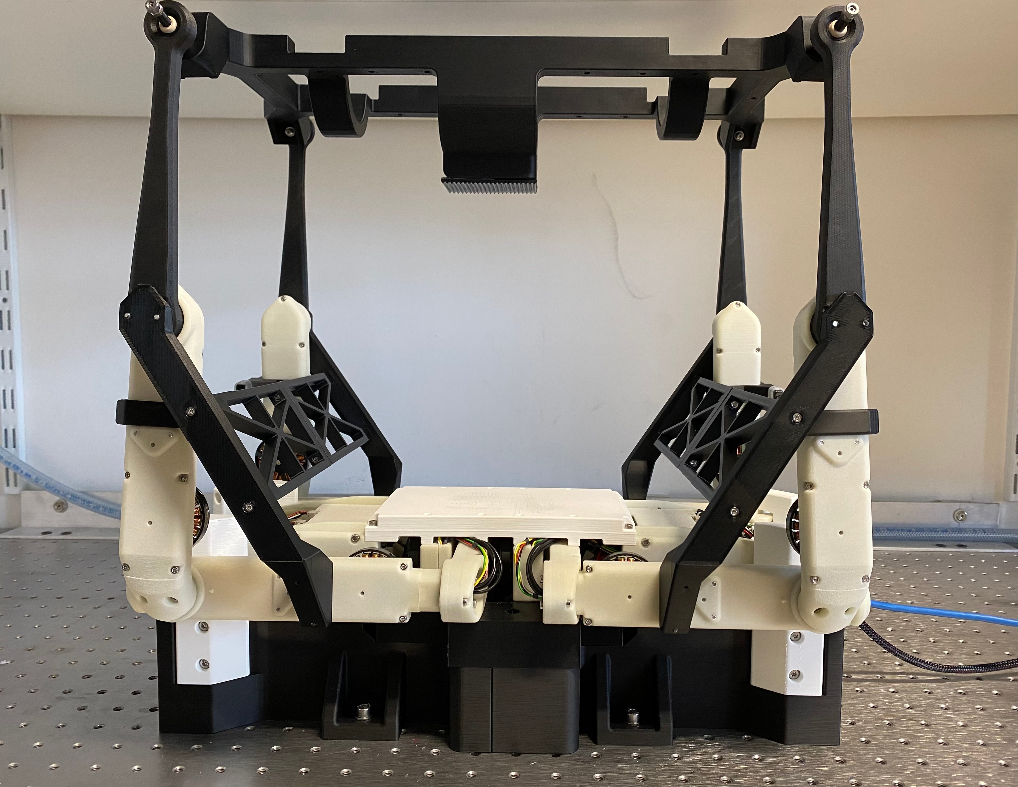
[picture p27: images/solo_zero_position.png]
    
</p>

#### Calibration position
Configuration of Robot when calibration tools are not attached and before starting Calibration Phase
<p align="center">
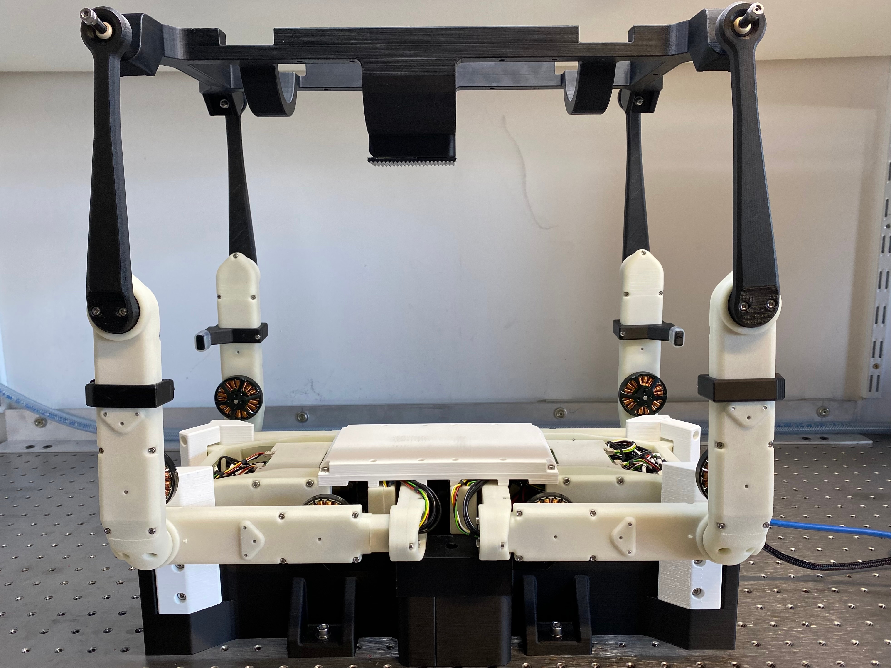
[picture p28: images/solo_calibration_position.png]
    
</p> 

#### Home position
Configuration of Robot when no sequence is given or when Robot is waiting for ADC trigger. 
<p align="center">
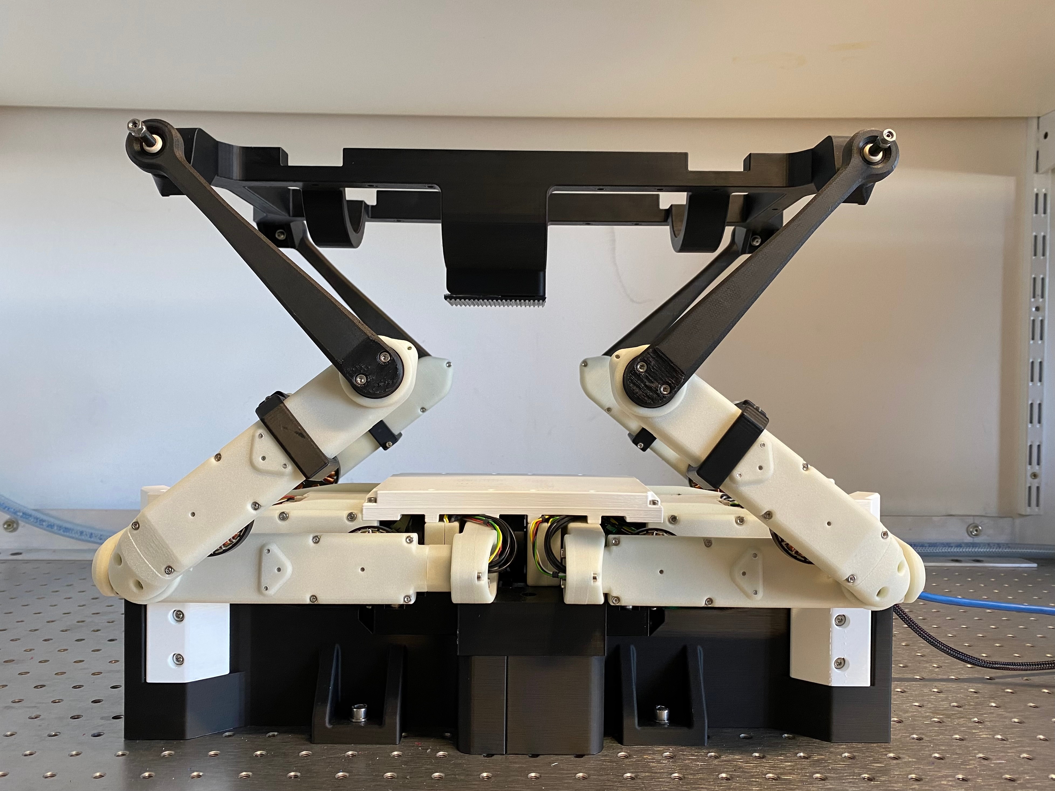
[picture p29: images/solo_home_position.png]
    
</p> 

#### Landing position
Configuration of Robot after completing smooth landing.
<p align="center">
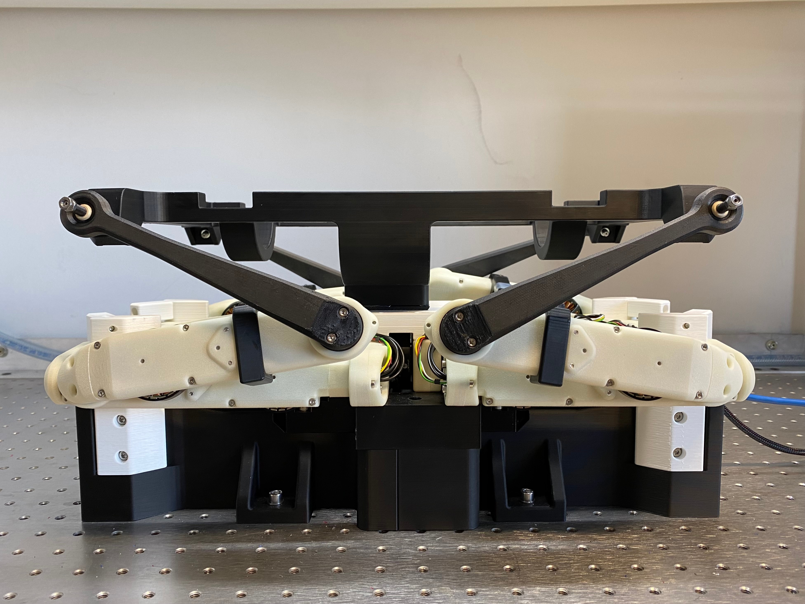
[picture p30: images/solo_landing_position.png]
    
</p> 

---

### Robot Behaviour and Usage
After completing the hardware and software setup, you are ready to use our SOLO 6 DoF Motion Platform. Refer to the [Program Execution](./program_execution.md) Section for starting and using the robot.  

A high level overview of the software steps and expected robot behaviour is as following:
1. Hardware Setup is completed (Refer to [Hardware Setup](#hardware-setup)). 
2. Software Setup is completed (Refer to [Software Setup](#software-setup)). 
3. Realtime OS Setup is completed (Refer to [Realtime OS Setup](#realtime-os-setup)).
4. Robot calibration phase 0 and calibration phase 1 are completed (refer to [Calibration Process](#calibration-process)).
5. The user runs a program with the SOLO control environemnt (refer to [Program Execution](./program_execution.md)).
6. If calibration phase 2 is not completed, the user runs calibration phase 2. Then the landing position is set (refer to [Calibration Position](#calibration-process). 
7. The user runs the program with calibration phase x from landing position.
8. From the landing position, the robot goes to home position (refer to [Robot Positions](robot-positions)) through a smooth linear interpolation trajectory. If the correct motor indices are not found, the home position has an offset and does not look like the image in [Robot Positions](robot-positions).
9. The robot stays in the home position and waits for the ADC button trigger signal. 
10. After receiving the ADC button trigger signal, the robot waits for 2 seconds as a safety mechanism. Then the robot starts to move our 6 DoF Motion Platform in the commanded motion trajectory. 
11. After completing the commanded motion trajectory, the robot places the motion platform in the landing position (refer to [Robot Positions](robot-positions)) through a smooth linear interpolation trajectory. 
12. The data will be processed (time of processing data depends on the runtime of the motion platform and length of commanded motion trajectory).
13. The processed data will be visualized through plots and graphs. 
14. The program ends.

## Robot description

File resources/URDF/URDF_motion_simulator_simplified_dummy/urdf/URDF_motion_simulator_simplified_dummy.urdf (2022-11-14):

<?xml version="1.0" encoding="utf-8"?>
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
<robot name="URDF_motion_simulator_simplified_dummy">
  <link name="base_link">
    <inertial>
      <origin xyz="-0.00378758182204412 0.032755494750085 3.55184467035811E-07" rpy="0 0 0" />
      <mass value="0.369358553365675" />
      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
    </inertial>
    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
  </link>
  <link name="hip_left_front">
    <inertial>
      <origin xyz="-0.00114777917617824 -3.9453711776459E-05 -0.0951126253066146" rpy="0 0 0" />
      <mass value="0.0464560424052731" />
      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
    </inertial>
    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
  </link>
  <joint name="hip_left_front" type="continuous">
    <origin xyz="0.0266 0.0875 0.031" rpy="-1.5707963267949 -0.0888684160670934 1.5707963267949" />
    <parent link="base_link" />
    <child link="hip_left_front" />
    <axis xyz="0 0 1" />
    <limit lower="0" upper="0" effort="0" velocity="0" />
  </joint>
  <link name="upper_leg_left_front">
    <inertial>
      <origin xyz="0.0335844560922996 -4.50009883709579E-05 -0.0812375723976322" rpy="0 0 0" />
      <mass value="0.0443837568086894" />
      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
    </inertial>
    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
  </link>
  <joint name="upper_leg_left_front" type="continuous">
    <origin xyz="0 0 -0.168" rpy="-1.61214157811801 0 0" />
    <parent link="hip_left_front" />
    <child link="upper_leg_left_front" />
    <axis xyz="-1 0 0" />
    <limit lower="0" upper="0" effort="0" velocity="0" />
  </joint>
  <link name="lower_leg_left_front">
    <inertial>
      <origin xyz="-0.0140069086189654 -3.22959387843991E-08 -0.0683745671961548" rpy="0 0 0" />
      <mass value="0.0320230637234883" />
      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
    </inertial>
    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
  </link>
  <joint name="lower_leg_left_front" type="continuous">
    <origin xyz="0.0451575365316773 0 -0.16" rpy="-0.0017453292519866 0 3.14159265358979" />
    <parent link="upper_leg_left_front" />
    <child link="lower_leg_left_front" />
    <axis xyz="1 0 0" />
    <limit lower="0" upper="0" effort="0" velocity="0" />
  </joint>
  <link name="dummy_left_front">
    <inertial>
      <origin xyz="1.94289029309402E-16 4.9960036108132E-16 -0.000594786724318619" rpy="0 0 0" />
      <mass value="4.18879020478639E-06" />
      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
    </inertial>
    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
  </link>
  <joint name="dummy_left_front" type="continuous">
    <origin xyz="-0.0142500238911007 0 -0.160052746822092" rpy="-1.659664742862 -0.0395999220711239 -1.5707963267949" />
    <parent link="lower_leg_left_front" />
    <child link="dummy_left_front" />
    <axis xyz="0 0 1" />
  </joint>
  <link name="hip_right_front">
    <inertial>
      <origin xyz="-0.00128328837930811 -4.41156613188269E-05 -0.0894544410841239" rpy="0 0 0" />
      <mass value="0.0415506938007008" />
      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
    </inertial>
    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
  </link>
  <joint name="hip_right_front" type="continuous">
    <origin xyz="0.0421999999999998 -0.0875 0.0310000000000001" rpy="1.5707963267949 -0.0888684160671074 -1.5707963267949" />
    <parent link="base_link" />
    <child link="hip_right_front" />
    <axis xyz="0 0 1" />
    <limit lower="0" upper="0" effort="0" velocity="0" />
  </joint>
  <link name="upper_leg_right_front">
    <inertial>
      <origin xyz="0.0335842661332895 -4.47898904026856E-05 -0.0812357114830771" rpy="0 0 0" />
      <mass value="0.0443850830836431" />
      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
    </inertial>
    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
  </link>
  <joint name="upper_leg_right_front" type="continuous">
    <origin xyz="0 0 -0.1524" rpy="1.61214157811801 0 0" />
    <parent link="hip_right_front" />
    <child link="upper_leg_right_front" />
    <axis xyz="-1 0 0" />
    <limit lower="0" upper="0" effort="0" velocity="0" />
  </joint>
  <link name="lower_leg_right_front">
    <inertial>
      <origin xyz="-0.0307978176908624 -2.77351331068321E-08 -0.0683745706192754" rpy="0 0 0" />
      <mass value="0.0320230612142886" />
      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
    </inertial>
    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
  </link>
  <joint name="lower_leg_right_front" type="continuous">
    <origin xyz="0.0283666271345778 0 -0.16" rpy="0.00174532925198727 0 -3.14159265358979" />
    <parent link="upper_leg_right_front" />
    <child link="lower_leg_right_front" />
    <axis xyz="1 0 0" />
    <limit lower="0" upper="0" effort="0" velocity="0" />
  </joint>
  <link name="dummy_right_front">
    <inertial>
      <origin xyz="8.53371171750383E-05 0.000161763066584331 0.00118091884280049" rpy="0 0 0" />
      <mass value="4.18879020478639E-06" />
      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
    </inertial>
    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
  </link>
  <joint name="dummy_right_front" type="continuous">
    <origin xyz="-0.0304430910633562 0 -0.16010597465947" rpy="-1.34906825918403 -0.0492173125903429 1.64177086104973" />
    <parent link="lower_leg_right_front" />
    <child link="dummy_right_front" />
    <axis xyz="0.0714119628942929 0.135366866036153 0.988218671719541" />
  </joint>
  <link name="hip_left_back">
    <inertial>
      <origin xyz="-0.00128328848757414 -4.41136000242613E-05 -0.0894544419441646" rpy="0 0 0" />
      <mass value="0.0415506942379489" />
      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
    </inertial>
    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
  </link>
  <joint name="hip_left_back" type="continuous">
    <origin xyz="-0.0422000000000003 0.0874999999999999 0.031" rpy="1.5707963267949 -0.088868416067085 1.5707963267949" />
    <parent link="base_link" />
    <child link="hip_left_back" />
    <axis xyz="0 0 1" />
    <limit lower="0" upper="0" effort="0" velocity="0" />
  </joint>
  <link name="upper_leg_left_back">
    <inertial>
      <origin xyz="0.0335842810737708 -4.48592050072694E-05 -0.0812358386973087" rpy="0 0 0" />
      <mass value="0.0443850097633001" />
      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
    </inertial>
    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
  </link>
  <joint name="upper_leg_left_back" type="continuous">
    <origin xyz="0 0 -0.1524" rpy="1.61214157811801 0 0" />
    <parent link="hip_left_back" />
    <child link="upper_leg_left_back" />
    <axis xyz="-1 0 0" />
    <limit lower="0" upper="0" effort="0" velocity="0" />
  </joint>
  <link name="lower_leg_left_back">
    <inertial>
      <origin xyz="-0.0140069083043222 -2.77293754624708E-08 -0.0683745697448815" rpy="0 0 0" />
      <mass value="0.0320230619709976" />
      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
    </inertial>
    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
  </link>
  <joint name="lower_leg_left_back" type="continuous">
    <origin xyz="0.0451575365316778 0 -0.16" rpy="0.00174532925198693 0 -3.14159265358979" />
    <parent link="upper_leg_left_back" />
    <child link="lower_leg_left_back" />
    <axis xyz="1 0 0" />
    <limit lower="0" upper="0" effort="0" velocity="0" />
  </joint>
  <link name="dummy_left_back">
    <inertial>
      <origin xyz="-2.77555756156289E-17 1.11022302462516E-16 -0.000594786724320312" rpy="0 0 0" />
      <mass value="4.18879020478639E-06" />
      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
    </inertial>
    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
  </link>
  <joint name="dummy_left_back" type="continuous">
    <origin xyz="-0.0142500238910989 0 -0.160052746822092" rpy="-1.65966474286198 0.0395999220711294 -1.5707963267949" />
    <parent link="lower_leg_left_back" />
    <child link="dummy_left_back" />
    <axis xyz="0 0 1" />
  </joint>
  <link name="hip_right_back">
    <inertial>
      <origin xyz="-0.00114777885671997 -3.94546783551199E-05 -0.0951126260332582" rpy="0 0 0" />
      <mass value="0.0464560462885094" />
      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
    </inertial>
    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
  </link>
  <joint name="hip_right_back" type="continuous">
    <origin xyz="-0.0266 -0.0875 0.031" rpy="-1.5707963267949 -0.0888684160668232 -1.5707963267949" />
    <parent link="base_link" />
    <child link="hip_right_back" />
    <axis xyz="0 0 1" />
    <limit lower="0" upper="0" effort="0" velocity="0" />
  </joint>
  <link name="upper_leg_right_back">
    <inertial>
      <origin xyz="0.033584399570773 -4.49615734106068E-05 -0.0812369288638612" rpy="0 0 0" />
      <mass value="0.0443841843830056" />
      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
    </inertial>
    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
  </link>
  <joint name="upper_leg_right_back" type="continuous">
    <origin xyz="0 0 -0.168" rpy="-1.61214157811801 0 0" />
    <parent link="hip_right_back" />
    <child link="upper_leg_right_back" />
    <axis xyz="-1 0 0" />
    <limit lower="0" upper="0" effort="0" velocity="0" />
  </joint>
  <link name="lower_leg_right_back">
    <inertial>
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

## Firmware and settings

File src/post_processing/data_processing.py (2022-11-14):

import csv
import numpy as np 
import matplotlib.pyplot as plt
import math
import argparse
from scipy.spatial.transform import Rotation
from scipy import signal
from scipy.signal import savgol_filter

import sys, os
sys.path.append('./')
from config import *
from post_processing.data_preview import DataPreviewClass

class DataProcessClass():

    def __init__(self, 
        name_of_data_csv=None,
        robot_env = '', # pybullet / solo
        point_on_platform = [0,0,0],
        raw_data_traj_platform = GLOBAL_AUTOGENERATED_DIRECTORY + TRAJ_PLATFORM_FILE_NAME,
        external_output_directory = "", # specify if you do not want to use config output directory
        external_output_file_name = "", # specify if you do not want to use config output directory
        save_data = True,
        save_history = True,
        update_data = False
    ):
        self.name_of_data_csv = name_of_data_csv 
        self.robot_env = robot_env
        self.point_on_platform = point_on_platform
        self.external_output_directory = external_output_directory
        self.external_output_file_name = external_output_file_name
        self.save_data = save_data
        self.save_history = save_history
        self.update_data = update_data

        if self.robot_env == '':
            print("Robot env not specified. Exiting!")
            exit(-1)
        
        self.init_fr_leg_params()

        print('Loading data...', end='\r')
        self.seq_num = []
        self.time_stamp = [] 
        self.curr_jointAngles = [] 
        self.target_jointAngles = []
        self.current_value = []
        self.platform_target = self.get_raw_data_from_csv(raw_data_traj_platform)
        self.platform_target = np.array(self.platform_target)
        if self.update_data:
            self.platform_target = self.platform_target[:,19:37]
        
        try:
            self.fill_values_from_csv()
        except:
            print("Unable to fill values from csv. Is csv empty? ==>", self.name_of_data_csv)
            exit(-1)

        print('Loading data...done')
        if self.robot_env == 'pybullet': 
            self.frequency = 240
            self.curr_jointAngles = self.map_motors_according_to_ctrl_robot(self.curr_jointAngles)
            self.target_jointAngles = self.map_motors_according_to_ctrl_robot(self.target_jointAngles)
            self.current_value = self.map_motors_according_to_ctrl_robot(self.current_value)
        elif self.robot_env == 'solo':
            self.frequency = 1000

        self.get_calculated_platform_vel_acc()

        if self.robot_env == 'solo':
            self.imu_data_transformation()

        self.save_calculated_platform_vel_acc()

      
    def init_fr_leg_params(self):
        """
            Initializes motor mapping and parameters for fr joint leg. 

            :return: None.
            :rtype: None.
        """
        self.iq_sat = 12
        self.imu_data = []
        self.motor_mapping = {
            "bl_hip" : 0,
            "br_hip" : 1,
            "bl_lower" : 2,
            "bl_upper" : 3,
            "br_lower" : 4,
            "br_upper" : 5,
            "fl_hip" : 6,
            "fr_hip" : 7,
            "fl_lower" : 8,
            "fl_upper" : 9,
            "fr_lower" : 10,
            "fr_upper" : 11,
            0 : "bl_hip",
            1 : "br_hip",
            2 : "bl_lower",
            3 : "bl_upper",
            4 : "br_lower",
            5 : "br_upper",
            6 : "fl_hip",
            7 : "fr_hip",
            8 : "fl_lower",
            9 : "fl_upper",
            10 : "fr_lower",
            11 : "fr_upper" 
        }
    

    def map_motors_according_to_ctrl_robot(self, values):
        """
            Maps PyBullet motor indices to solo robot motor indices. 

            :param values: Motor values with motor index following PyBullet motor index convention.
            :type values: ndarray.
            :return: Updated motor values with motor index following SOLO robot motor index convention.
            :rtype: ndarray.
        """
        values = np.array(values)

        if len(values.T) != 12 and len(values.T) != 16:
            print("Number of joint positions != 12 or 16. Exiting!")
            exit(-1) 

        if len(values.T) == 16: # removing dummy joints if input
            dummy_joints = [3,7,11,15]
            updated_values = []
            for v in values:
                temp = []
                for ti, tv in enumerate(v):
                    if ti in dummy_joints:
                        continue
                    else:
                        temp.append(tv)
                updated_values.append(temp)
        
            values = updated_values
        
        mapped_values = []
        for value in values:
            mapped_value = [None] * 12
            mapped_value[self.motor_mapping["bl_hip"]] = - value[6] # bl_hip = hip_left_back 
            mapped_value[self.motor_mapping["br_hip"]] = value[9] # br_hip = hip_right_back
            mapped_value[self.motor_mapping["bl_lower"]] = value[8] # bl_lower = lower_leg_left_back
            mapped_value[self.motor_mapping["bl_upper"]] = value[7] # bl_upper = upper_leg_left_back
            mapped_value[self.motor_mapping["br_lower"]] = value[11] # br_lower = lower_leg_right_back
            mapped_value[self.motor_mapping["br_upper"]] = value[10] # br_upper = upper_leg_right_back
            mapped_value[self.motor_mapping["fl_hip"]] = value[0] # fl_hip = hip_left_front
            mapped_value[self.motor_mapping["fr_hip"]] = - value[3] # fr_hip = hip_right_front
            mapped_value[self.motor_mapping["fl_lower"]] = value[2] # fl_lower = lower_leg_left_front
            mapped_value[self.motor_mapping["fl_upper"]] = value[1] # fl_upper = upper_leg_left_front
            mapped_value[self.motor_mapping["fr_lower"]] = value[5] # fr_lower = lower_leg_right_front
            mapped_value[self.motor_mapping["fr_upper"]] = value[4] # fr_upper = upper_leg_right_front
            mapped_values.append(mapped_value)
        return np.array(mapped_values)

    
    def fill_values_from_csv(self):
        """
            Fills values from csv file. 

            :return: None.
            :rtype: None.
        """
        raw_data = np.array(self.get_raw_data_from_csv(self.name_of_data_csv, header=True))

        if self.name_of_data_csv == GLOBAL_OUTPUT_DIRECTORY + PYBULLET_DATA_OUTPUT_FILE_NAME:
            self.seq_num = raw_data[:, 0]
            self.time_stamp = self.seq_num
            self.curr_jointAngles = raw_data[:, 1 : 17]
            self.target_jointAngles = raw_data[:, 17 : 33]     
            self.current_value = raw_data[:, 33 : 49]   
  
        else:
            self.time_stamp = raw_data[:-TIME_INTERPOLATE_LANDING+1, 0]
            self.time_stamp = self.time_stamp - self.time_stamp[0] # correct timestamp
            self.curr_jointAngles = raw_data[:-TIME_INTERPOLATE_LANDING+1, 1 : 13]
            self.target_jointAngles = raw_data[:-TIME_INTERPOLATE_LANDING+1, 13 : 25]
            self.current_value = raw_data[:-TIME_INTERPOLATE_LANDING+1, 25 : 37]
            self.imu_data = raw_data[:-TIME_INTERPOLATE_LANDING+1, 37 : 49]
         

    def get_raw_data_from_csv(self, name_of_csv_file, header=True):
        """
            Returns raw data from any csv file. 

            :param name_of_data_csv_file: Name of csv file.
            :type name_of_data_csv_file: str.
            :param header: Specify whether csv file have header or not.
            :type header: Bool.
            :return: Returns list of rows from csv file.
            :rtype: List[List[Float]].
        """
        f = open(name_of_csv_file)
        csv_reader = csv.reader(f)
        data = [] 
        header_skipped = False 
        for line in csv_reader:
            temp = []
            if not header_skipped and header:
                header_skipped = True 
                continue 
            for e in line:
                try:
                    temp.append(float(e))
                except:
                    temp.append(e)
            data.append(temp)
        return data 


    def get_calculated_platform_vel_acc(self):
        """
            Gets calculated position, velocity, and acceleration for platform using forward kinematics. 

            :return: None.
            :rtype: None.
        """
        self.init_params_for_calculations()
        self.calculate_platform_vel_acc()

    
    def save_calculated_platform_vel_acc(self):
        """
            Saves calculated platform position, velocity, and acceleration.

            :return: None.
            :rtype: None.
        """
        if self.robot_env == 'solo':
            self.save_output_file_name = GLOBAL_OUTPUT_DIRECTORY + SOLO_CALCULATED_FILE_NAME
            if self.external_output_directory == "":
                self.save_output_file_name_c = GLOBAL_OUTPUT_DIRECTORY + HISTORY_DIR + SOLO_CALCULATED_FILE_UNIQUE
            else:
                self.save_output_file_name_c = self.external_output_directory + self.external_output_file_name
        elif self.robot_env == 'pybullet':
            self.save_output_file_name = GLOBAL_OUTPUT_DIRECTORY + PYBULLET_CALCULATED_FILE_NAME
            if self.external_output_directory == "":
                self.save_output_file_name_c = GLOBAL_OUTPUT_DIRECTORY + HISTORY_DIR + PYBULLET_CALCULATED_FILE_UNIQUE
            else:
                self.save_output_file_name_c = self.external_output_directory + self.external_output_file_name
        if self.save_data:
            self.save_f = open(self.save_output_file_name, 'w')
        if self.save_history:
            self.save_f_c = open(self.save_output_file_name_c, 'w')

        if self.robot_env == 'solo':
            header = ['t', 
                        'lx', 'ly', 'lz', 
                        'ax', 'ay', 'az', 
                        'lvx', 'lvy', 'lvz', 
                        'avx', 'avy', 'avz', 
                        'lax', 'lay', 'laz',
                        'aax', 'aay', 'aaz',
                        'target_lx', 'target_ly', 'target_lz', 
                        'target_ax', 'target_ay', 'target_az',
                        'target_lvx', 'target_lvy', 'target_lvz', 
                        'target_avx', 'target_avy', 'target_avz', 
                        'target_lax', 'target_lay', 'target_laz',
                        'target_aax', 'target_aay', 'target_aaz',
                        'transformed_lax', 'transformed_lay', 'transformed_laz',
                        'transformed_aax', 'transformed_aay', 'transformed_aaz'
                    ] 
        elif self.robot_env == 'pybullet': # no transformed IMU data
            header = ['t', 
                        'lx', 'ly', 'lz', 
                        'ax', 'ay', 'az', 
                        'lvx', 'lvy', 'lvz', 
                        'avx', 'avy', 'avz', 
                        'lax', 'lay', 'laz',
                        'aax', 'aay', 'aaz',
                        'target_lx', 'target_ly', 'target_lz', 
                        'target_ax', 'target_ay', 'target_az',
                        'target_lvx', 'target_lvy', 'target_lvz', 
                        'target_avx', 'target_avy', 'target_avz', 
                        'target_lax', 'target_lay', 'target_laz',
                        'target_aax', 'target_aay', 'target_aaz',
                    ] 

        if self.save_data:
            self.data_writer = csv.writer(self.save_f)
            self.data_writer.writerow(header)
        if self.save_history:
            self.data_writer_c = csv.writer(self.save_f_c)
            self.data_writer_c.writerow(header)

        if self.save_data or self.save_history:
            for i in range(len(self.time_stamp)):
                tr = [] 
                tr.append(self.time_stamp[i])
                for j in range(3):
                    tr.append(self.platform_pos_calc[i][j])
                for j in range(3):
                    tr.append(self.platform_ang_calc[i][j])
                for j in range(3):
                    tr.append(self.platform_lin_vel_calc[i][j])
                for j in range(3):
                    tr.append(self.platform_ang_vel_calc[i][j])
                for j in range(3):
                    tr.append(self.platform_lin_acc_calc[i][j])
                for j in range(3):
                    tr.append(self.platform_ang_acc_calc[i][j])
                
                for j in range(3):
                    tr.append(self.platform_pos[i][j])
                for j in range(3):
                    tr.append(self.platform_ang[i][j])
                for j in range(3):
                    tr.append(self.platform_lin_vel[i][j])
                for j in range(3):
                    tr.append(self.platform_ang_vel[i][j])
                for j in range(3):
                    tr.append(self.platform_lin_acc[i][j])
                for j in range(3):
                    tr.append(self.platform_ang_acc[i][j])

                if self.robot_env == 'solo':
                    for j in range(3):
                        tr.append(self.transformted_lin_acc_imu_data[i][j])
                    for j in range(3):
                        tr.append(self.imu_calc_angular_acceleration[i][j])
                
                if self.save_data:
                    self.data_writer.writerow(tr)   
                if self.save_history:
                    self.data_writer_c.writerow(tr)    
        
        if self.save_data:
            self.save_f.close()
            print("Saved Ouptut in file:",self.save_output_file_name)

        if self.save_history:
            self.save_f_c.close()
            print("Saved Ouptut in file:",self.save_output_file_name_c)


    def normalizeVector(self, vec):
        """
            Returns normalized vector.

            :param vec: Vector you want to normalize.
            :type vec: np.array([]).
            :return: Normalized vector.
            :rtype: ndarray.
        """
        return vec / np.linalg.norm(vec)

    
    def calculate_platform_vel_acc(self): 
        """
            Calculates position, velocity, and acceleration for platform using forward kinematics. 

            :return: None.
            :rtype: None.
        """
        # Convert all vectors to Z up system
        rotMatrix = Rotation.from_euler('xyz', [math.pi/2, 0, 0], degrees=False).as_matrix()
        self.vec_base = rotMatrix.dot(self.vec_base)
        self.vec_hip = rotMatrix.dot(self.vec_hip)
        self.vec_u_leg = rotMatrix.dot(self.vec_u_leg)
        self.vec_l_leg = rotMatrix.dot(self.vec_l_leg)

        progress = 0
        print('Calculating positions and orientations...', progress, '%', end='\r')
        # calculation of platform position
        for ti, current_motor_pos in enumerate(self.curr_jointAngles):
            progress = math.floor(ti/len(self.curr_jointAngles) * 100)
            print('Calculating positions and orientations...', progress, '%', end='\r')
            points = []
            points.append(self.calculateBallJointPosition([6,9,8], 'left_front', current_motor_pos))
            points.append(self.calculateBallJointPosition([7,11,10], 'right_front', current_motor_pos))
            points.append(self.calculateBallJointPosition([0,3,2], 'left_back', current_motor_pos))
            points.append(self.calculateBallJointPosition([1,5,4], 'right_back', current_motor_pos))
            
            vcross1 = points[3] - points[0]
            vcross2 = points[2] - points[1]

            vx = self.normalizeVector(points[0] - points[2])
            vy = self.normalizeVector(points[0] - points[1])
            vz = self.normalizeVector(np.cross(vcross2, vcross1))

            # calculate acceleration
            self.platform_curr_pos = points[0] + vcross1/2 - np.array([0, 0, 6.73])/1000 # assumed that the middle point is also the middle of the platform
            rotMatrix = Rotation.align_vectors([[1, 0, 0], [0, 1, 0], [0, 0, 1]], [vx, vy, vz])[0].as_matrix()
            rotMatrix = rotMatrix.transpose()
            
            self.platform_curr_ang = Rotation.from_matrix(rotMatrix).as_euler('xyz', degrees=False)
            self.platform_curr_pos = np.array(self.platform_curr_pos) + rotMatrix.dot(self.point_on_platform)
        
            self.platform_pos_calc.append(self.platform_curr_pos)
            self.platform_ang_calc.append(self.platform_curr_ang)
        
        if not self.update_data:
            self.platform_pos.append(self.platform_target[:, :3])
            self.platform_ang.append(self.platform_target[:, 3:])
            self.platform_pos = self.platform_pos[0]
            self.platform_ang = self.platform_ang[0]
        else:
            self.platform_pos = self.platform_target[:, :3]
            self.platform_ang = self.platform_target[:, 3:6]

        print('Calculating positions and orientations...done   ')

        self.platform_pos_calc_raw = self.platform_pos_calc
        self.platform_ang_calc_raw = self.platform_ang_calc

        # filter position data
        print('Filtering position data...', end='\r')
        # self.find_cutoff_frequency(self.platform_pos_calc)
        self.platform_pos_calc = self.filter_data(self.platform_pos_calc)
        fc_lin = self.fc
        print('Filtering position data...done (cutoff frequency:', fc_lin, 'Hz)')

        print('Filtering orientation data...', end='\r')
        # self.find_cutoff_frequency(self.platform_ang_calc)
        self.platform_ang_calc = self.filter_data(self.platform_ang_calc)
        fc_ang = self.fc
        print('Filtering orientation data...done (cutoff frequency:', fc_ang, 'Hz)')
        # calculation of platform velocity
        for i in range(len(self.platform_pos_calc)):
            if i == 0:
                self.platform_curr_lin_vel = np.array([0,0,0])
                self.platform_curr_ang_vel = np.array([0,0,0])
                if not self.update_data:
                    self.platform_lin_vel.append(np.array([0,0,0]))
                    self.platform_ang_vel.append(np.array([0,0,0]))
                else:
                    self.platform_lin_vel = self.platform_target[:, 6:9]
                    self.platform_ang_vel = self.platform_target[:, 9:12]

            else:
                self.platform_curr_lin_vel = self.xyz_derivative(self.platform_pos_calc[i - 1], self.platform_pos_calc[i], self.dt)
                self.platform_curr_ang_vel = self.xyz_derivative(self.platform_ang_calc[i - 1], self.platform_ang_calc[i], self.dt)
                if not self.update_data:
                    self.platform_lin_vel.append(self.xyz_derivative(self.platform_pos[i - 1], self.platform_pos[i], self.dt))
                    self.platform_ang_vel.append(self.xyz_derivative(self.platform_ang[i - 1], self.platform_ang[i], self.dt))
            
            self.platform_lin_vel_calc.append(self.platform_curr_lin_vel)          
            self.platform_ang_vel_calc.append(self.platform_curr_ang_vel)          

        self.platform_lin_vel_calc_raw = self.platform_lin_vel_calc
        self.platform_ang_vel_calc_raw = self.platform_ang_vel_calc
        
        # filter velocity data
        print('Filtering linear velocity data...', end='\r')
        self.fc = fc_lin
        self.platform_lin_vel_calc = self.filter_data(self.platform_lin_vel_calc)
        print('Filtering linear velocity data...done')

        print('Filtering angular velocity data...', end='\r')
        self.fc = fc_ang
        self.platform_ang_vel_calc = self.filter_data(self.platform_ang_vel_calc)
        print('Filtering angular velocity data...done')        
            
        # calculation of platform acceleration
        for i in range(len(self.platform_lin_vel_calc)):
            if i == 0 or i == 1:
                self.platform_curr_lin_acc = np.array([0,0,0])
                self.platform_curr_ang_acc = np.array([0,0,0])
                if not self.update_data:
                    self.platform_lin_acc.append(np.array([0,0,0]))
                    self.platform_ang_acc.append(np.array([0,0,0]))
                else:
                    self.platform_lin_acc = self.platform_target[:, 12:15]
                    self.platform_ang_acc = self.platform_target[:, 15:18]
        
            else:
                self.platform_curr_lin_acc = self.xyz_derivative(self.platform_lin_vel_calc[i - 1], self.platform_lin_vel_calc[i], self.dt)
                self.platform_curr_ang_acc = self.xyz_derivative(self.platform_ang_vel_calc[i - 1], self.platform_ang_vel_calc[i], self.dt)
                if not self.update_data:
                    self.platform_lin_acc.append(self.xyz_derivative(self.platform_lin_vel[i - 1], self.platform_lin_vel[i], self.dt))
                    self.platform_ang_acc.append(self.xyz_derivative(self.platform_ang_vel[i - 1], self.platform_ang_vel[i], self.dt))

            self.platform_lin_acc_calc.append(self.platform_curr_lin_acc)          
            self.platform_ang_acc_calc.append(self.platform_curr_ang_acc)          

        self.platform_lin_acc_calc_raw = self.platform_lin_acc_calc
        self.platform_ang_acc_calc_raw = self.platform_ang_acc_calc

        # filter acceleration data
        print('Filtering linear acceleration data...', end='\r')
        self.fc = fc_lin
        self.platform_lin_acc_calc = self.filter_data(self.platform_lin_acc_calc)
        print('Filtering linear acceleration data...done')

        print('Filtering angular acceleration data...', end='\r')
        self.fc = fc_ang
        self.platform_ang_acc_calc = self.filter_data(self.platform_ang_acc_calc)
        print('Filtering angular acceleration data...done')

        self.platform_sys_time = self.time_data

        index = 0
        self.platform_lin_acc_calc = np.array(self.platform_lin_acc_calc)
        self.platform_lin_acc_calc_raw = np.array(self.platform_lin_acc_calc_raw)
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

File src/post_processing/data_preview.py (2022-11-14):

"""
    Python script to preview stored data
"""

import csv
import numpy as np 
import matplotlib.pyplot as plt
import math
import argparse
import sys, os
sys.path.append('./')
from config import *

class DataPreviewClass():

    def __init__(self, 
        name_of_data_csv_file=None,
        name_of_calculated_csv_file=None,
        robot_env = '',                             # pybullet / solo
        plot_fr_joint_angles = False,               # for joint angles of front right leg
        plot_calculated_pos_data = False,           # for calculated pos
        plot_calculated_vel_data = False,           # for calculated vel
        plot_calculated_acc_data = False,           # for calculated acc
        plot_imu_data = False,                      # for imu data
        plot_circular_traj_platform = False,        # for circular trajectory platform plot
        plot_combined_pose_graph = False,           # for combined 6x3 pose graph
        plot_x_min = None,                          # for x min in x-axis
        plot_x_max = None                           # for x max in x-axis
    ):
        self.name_of_data_csv_file = name_of_data_csv_file 
        self.name_of_calculated_csv_file = name_of_calculated_csv_file 
        self.robot_env = robot_env
        self.plot_fr_joint_angles = plot_fr_joint_angles
        self.plot_calculated_pos_data = plot_calculated_pos_data
        self.plot_calculated_vel_data = plot_calculated_vel_data
        self.plot_calculated_acc_data = plot_calculated_acc_data
        self.plot_imu_data = plot_imu_data
        self.plot_circular_traj_platform = plot_circular_traj_platform
        self.plot_combined_pose_graph = plot_combined_pose_graph
        self.plot_x_min = int(plot_x_min) if plot_x_min is not None else None
        self.plot_x_max = int(plot_x_max) if plot_x_max is not None else None

        self.imu_data = None

        self.global_g = 9.81

        if self.robot_env == '':
            print("Robot env not specified. Exiting!")
            exit(-1)

        print('Loading data...', end='\r')

        if self.plot_fr_joint_angles or self.plot_imu_data or self.plot_calculated_vel_data or self.plot_calculated_acc_data or self.plot_calculated_pos_data or self.plot_circular_traj_platform:
            if self.plot_fr_joint_angles:self.init_fr_leg_params()
            try:
                if self.plot_fr_joint_angles:self.fill_values_from_data_csv()
                self.fill_values_from_calculated_csv()
            except Exception as e:
                print("Unable to fill values from csv. Is csv empty? ==>", self.name_of_data_csv_file)
                print("Excpetion:", e)
                exit(-1)

        print('Loading data...done')

        if self.robot_env == 'pybullet': 
            self.frequency = 240
            if self.plot_fr_joint_angles:
                self.curr_jointAngles = self.map_motors_according_to_ctrl_robot(self.curr_jointAngles)
                self.target_jointAngles = self.map_motors_according_to_ctrl_robot(self.target_jointAngles)
                self.current_value = self.map_motors_according_to_ctrl_robot(self.current_value)
        elif self.robot_env == 'solo':
            self.frequency = 1000

        print("Plotting...", end='\r')
        if self.plot_fr_joint_angles: self.fr_joint_angles_plotter()
        if self.plot_calculated_pos_data: self.calculated_pos_data_plotter()
        if self.plot_calculated_vel_data: self.calculated_vel_data_plotter()
        if self.plot_calculated_acc_data: self.calculated_acc_data_plotter()
        if self.plot_imu_data: self.raw_imu_data_plotter()
        if self.plot_circular_traj_platform: self.circular_traj_platform_plotter()
        if self.plot_combined_pose_graph: self.combined_pose_graph_v()
 
        print("Plotting...done")
        plt.show()
        print("Completed!")


    def fill_values_from_calculated_csv(self):
        """
            Fills calculated data values from csv file. 

            :return: None.
            :rtype: None.
        """
        raw_data = np.array(self.get_raw_data_from_csv(self.name_of_calculated_csv_file, header=True))
        
        self.platform_sys_time = raw_data[:, 0]
        self.platform_pos_calc = raw_data[:, 1 : 4]
        self.platform_ang_calc = raw_data[:, 4: 7]
        self.platform_lin_vel_calc = raw_data[:, 7: 10]
        self.platform_ang_vel_calc = raw_data[:, 10: 13]
        self.platform_lin_acc_calc = raw_data[:, 13: 16]
        self.platform_ang_acc_calc = raw_data[:, 16: 19]
        self.platform_pos = raw_data[:, 19 : 22]
        self.platform_ang = raw_data[:, 22: 25]

        self.platform_lin_vel = raw_data[:, 25 : 28]
        self.platform_ang_vel = raw_data[:, 28: 31]
        self.platform_lin_acc = raw_data[:, 31 : 34]
        self.platform_ang_acc = raw_data[:, 34: 37]

        self.transformted_lin_acc_imu_data = raw_data[:, 37 : 40]
        self.imu_calc_angular_acceleration = raw_data[:, 40 : 43]


    def init_fr_leg_params(self):
        """
            Initializes motor mapping and parameters for fr joint leg. 

            :return: None.
            :rtype: None.
        """
        self.motor_mapping = {
            "bl_hip" : 0,
            "br_hip" : 1,
            "bl_lower" : 2,
            "bl_upper" : 3,
            "br_lower" : 4,
            "br_upper" : 5,
            "fl_hip" : 6,
            "fr_hip" : 7,
            "fl_lower" : 8,
            "fl_upper" : 9,
            "fr_lower" : 10,
            "fr_upper" : 11,
            0 : "bl_hip",
            1 : "br_hip",
            2 : "bl_lower",
            3 : "bl_upper",
            4 : "br_lower",
            5 : "br_upper",
            6 : "fl_hip",
            7 : "fr_hip",
            8 : "fl_lower",
            9 : "fl_upper",
            10 : "fr_lower",
            11 : "fr_upper" 
        }
        self.iq_sat = 12
        self.seq_num = []
        self.time_stamp = [] 
        self.curr_jointAngles = [] 
        self.target_jointAngles = []
        self.current_value = []
    

    def map_motors_according_to_ctrl_robot(self, values):
        """
            Maps PyBullet motor indices to solo robot motor indices. 

            :param values: Motor values with motor index following PyBullet motor index convention.
            :type values: ndarray.
            :return: Updated motor values with motor index following SOLO robot motor index convention.
            :rtype: ndarray.
        """
        values = np.array(values)

        if len(values.T) != 12 and len(values.T) != 16:
            print("Number of joint positions != 12 or 16. Exiting!")
            exit(-1)
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

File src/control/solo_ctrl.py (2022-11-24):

"""
    Python script for solo control. 
"""

import math
import os
import csv
from scipy.interpolate import interp1d
import numpy as np
from config import *
import time
from control.free_solo_ctrl import *

try:
    import libmaster_board_sdk_pywrap as mbs
except ImportError:
    # print("- Cannot find libmaster_board_sdk_pywrap. PyBullet Simulation will work as normal but SOLO control will not work.")
    pass 

class SoloControlClass():

    def __init__(self,
        name_interface = 'enp9s0f1',
        n_slaves = 6,
        csv_joint_positions_file_name = TRAJ_JOINTS_FILE_NAME,
        solo_output_file = SOLO_DATA_OUTPUT_FILE_NAME,
        phase_0_calibration = False,
        phase_1_calibration = False,
        phase_2_calibration = False,
    ):
        self.debug_mode = False
        self.counter = 0 
        self.current_time = 0
        self.frequency = 1000 # Control frequency
        self.dt = 1/self.frequency #  Time step
        self.n_slaves = n_slaves
        self.phase_0_calibration = phase_0_calibration
        self.phase_1_calibration = phase_1_calibration
        self.phase_2_calibration = phase_2_calibration
        self.name_interface = name_interface
        self.csv_joint_positions_file_name = GLOBAL_AUTOGENERATED_DIRECTORY+csv_joint_positions_file_name
        self.solo_output_file = GLOBAL_OUTPUT_DIRECTORY+solo_output_file
        self.unique_solo_output_file = GLOBAL_OUTPUT_DIRECTORY + HISTORY_DIR + SOLO_DATA_OUTPUT_FILE_UNIQUE

        self.init_starting_params()
        if self.phase_0_calibration:
            self.init_masterboard_params()
            print("PHASE 0 Calibration. Motors and masterboard initialized. Exiting... \nRun Phase 1 with -c flag. \nRun Phase 2 with -v flag. \nRun sequences using calibrated parameters with no flag.\nEnd of program.")
            exit(1)

        self.sequence_motion_trajectory = self.load_trajectory(self.csv_joint_positions_file_name)
        self.init_constant_positions_joint_angles() # loads smooth_home_pos and smooth_landing_pos

        if self.phase_1_calibration:
            self.phase_2_calibration = False 
        
        if not self.phase_1_calibration and not phase_2_calibration:
            print("Loading Phase 2 Calibration Indices.")
            self.load_calibrated_zero_angles = True 
        else:
            if self.phase_1_calibration:
                print("Running Phase 1 Calibration")
            else:
                print("Running Phase 2 Calibration")
            self.load_calibrated_zero_angles = False 

        self.init_masterboard_params()
        self.init_controller_params()

        if self.phase_1_calibration or self.phase_2_calibration:      
            self.init_calibration()

        self.main_loop()

        self.robot_if.Stop()  # Shut down the interface between the computer and the master board

        print('---')

        if self.robot_if.IsTimeout():
            print("Masterboard timeout detected.")
            print("Either the masterboard has been shut down or there has been a connection issue with the cable/wifi.")

    
    def main_loop(self):
        """
            Main execution block. Runs until robot is not timeout. Maintains frequency of 1000 Hz.
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

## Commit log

2022-11-14 Adding framework flowchart
2022-11-14 Adding pkg resources
    [URDF_motion_simulator_simplified_dummy.csv, URDF_motion_simulator_simplified_dummy.urdf, URDF_sensor_platform_simplified.csv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]
2022-11-14 Adding src files
    [input_arbitrary.csv, input_circ.csv, input_sine.csv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]
2022-11-14 Adding PyBullet Inverse Kinematics
2022-11-15 Adding hardware framework doc
2022-11-15 Adding software framework doc
2022-11-15 Updating software framework
2022-11-15 Updating hardware framework doc
2022-11-15 Adding imu overlay example image
2022-11-16 Adding calibration position image
2022-11-16 Adding landing position image
2022-11-17 Updating hardware framework
2022-11-23 Create calibration_and_usage
2022-11-24 Adding free solo control for debugging and calibration using solo robot
2023-03-11 upload CAD model
    [Body1.SLDPRT, IGUS_KGLM-05_inner_shell.SLDPRT, calibration_platform.SLDPRT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]
